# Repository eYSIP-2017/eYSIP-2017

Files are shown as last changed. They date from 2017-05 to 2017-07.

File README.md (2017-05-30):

# eYSIP-2017_DistributedRobotics
## Project Title: 
Distributed Robotic - Multi Swarm Robots

## Project Description:
Understanding the behaviour of swarm robots and swarm intelligence. Building of swarm robots and displaying collective intelligence.

## Problem definition:
Using the swarm robots make the desired shapes of Alphabets. 

## Team: 
### Mentors: 
Ms. Rutuja and Ms. Deepa
### Members: 
Mr. R Hariharan and Mr. Chinmay

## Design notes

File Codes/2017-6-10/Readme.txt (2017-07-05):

The code was a trial to see switching of IR proximity sensor

Platform used : Firebird V (Nex Robotics)

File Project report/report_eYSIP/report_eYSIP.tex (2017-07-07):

\documentclass[a4paper,12pt,oneside]{book}

%-------------------------------Start of the Preable------------------------------------------------
\usepackage[english]{babel}
\usepackage{blindtext}
%packagr for hyperlinks
\usepackage{hyperref}
\hypersetup{
    colorlinks=true,
    linkcolor=blue,
    filecolor=magenta,      
    urlcolor=cyan,
}

\urlstyle{same}
%use of package fancy header
\usepackage{fancyhdr}
\setlength\headheight{26pt}
\fancyhf{}
%\rhead{\includegraphics[width=1cm]{logo}}
\lhead{\rightmark}
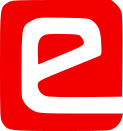
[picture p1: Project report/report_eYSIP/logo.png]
\rhead{}
\fancyfoot[RE, RO]{\thepage}
\fancyfoot[CE, CO]{\href{http://www.e-yantra.org}{www.e-yantra.org}}

\pagestyle{fancy}

%use of package for section title formatting
\usepackage{titlesec}
\titleformat{\chapter}
  {\Large\bfseries} % format
  {}                % label
  {0pt}             % sep
  {\huge}           % before-code
 
%use of package tcolorbox for colorful textbox
\usepackage[most]{tcolorbox}
\tcbset{colback=cyan!5!white,colframe=cyan!75!black,halign title = flush center}

\newtcolorbox{mybox}[1]{colback=cyan!5!white,
colframe=cyan!75!black,fonttitle=\bfseries,
title=\textbf{\Large{#1}}}

%use of package marginnote for notes in margin
\usepackage{marginnote}
\usepackage{tabularx}
%use of packgage watermark for pages
%\usepackage{draftwatermark}
%\SetWatermarkText{\includegraphics{logo}}
\usepackage[scale=2,opacity=0.1,angle=0]{background}
\backgroundsetup{
contents={}
}

%use of newcommand for keywords color
\usepackage{xcolor}
\newcommand{\keyword}[1]{\textcolor{red}{\textbf{#1}}}

%package for inserting pictures
\usepackage{graphicx}

%package for highlighting
\usepackage{color,soul}

%new command for table
\newcommand{\head}[1]{\textnormal{\textbf{#1}}}

%----------------------End of the Preamble---------------------------------------

\begin{document}

%---------------------Title Page------------------------------------------------
\begin{titlepage}
\raggedright
{\Large eYSIP2017\\[1cm]}
{\Huge\scshape\centering Distributed robotics - multi swarm robots \\[.1in]}
\vfill
\hfill\\
\begin{figure}[h!]
	\centering		
\end{figure}	
\hfill\\
\begin{flushright}
{\large Intern 1 Mr. Chinmay C \\}
{\large Intern 2 Mr. R Hariharan \\}
{\large Mentor 1 Ms. Rutuja \\}
{\large Mentor 2 Ms. Deepa \\}
{\large Duration of Internship: $ 22/05/2017-07/07/2017 $ \\}
\end{flushright}

{\itshape 2017, e-Yantra Publication}
\end{titlepage}
%-------------------------------------------------------------------------------

\tableofcontents

\chapter[Distributed robotics - multi swarm robots Hardware manual]{Distributed robotics - multi swarm robots Hardware manual}
\section{Abstract}
Swarm robotics is a field in robotics which implements coordination of multi robot systems which consist of large number of robots having simpler robots. There is a collective behavior that emerges from interactions between robots and interactions of robots with the environment. This behavior is emerged from field of biological studies of fishes, birds, ants, insects, etc. Application of swarm robotics varies from military, aviation to collective behavior of self driving cars. The objective of the project was to build miniaturized swarm bots and develop an algorithm for generic shape formation.

\subsection*{Following points are completed:}
\begin{itemize}
\item Study the concepts of swarm robotics and get familiar
with different robots available 
\item Study the kinematics of differential drive configuration 
\item Selecting appropriate sensors to be added 
\item Designing the PCB 
\item Assembling all the components 
\item Making of Mini bots 
\item Testing of Mini bots
\item Implementing circle formation of asynchronous fat robots with limited visibility in V-REP simulator
\item Developing and implementing generic shape formation algorithm for a system of distributed robots in V-REP simulator
\item Implementing follow the leader swarm behavior on Mini bots
\item Implementing rendezvous swarm behavior on Firebird V robots
\end{itemize}

\chapter[Hardware parts]{Hardware parts}
\begin{itemize}
  \item List of all hardware components are available \href{./COMPONENT LIST/Small_robot_PCB_schematic_WITH_COST.pdf}{here} 
  \item Microcontroller Atmega16 \href{./datasheet/atmega16.pdf}{Datasheet}, {Chip component, Lamington road, Mumbai} 
  \item Hex buffer CD40106 \href{./datasheet/CD40106.pdf}{Datasheet}, {Chip component, Lamington road, Mumbai} 
  \item Motor driver L293D \href{./datasheet/L293.pdf}{Datasheet}, {GALA Electronics, Lamington road, Mumbai} 
  \item Comparator LM158 \href{./datasheet/lm158-n.pdf}{Datasheet}, {Chip component, Lamington road, Mumbai}
  \item Actuators BO motors: 60 rpm 12 volts	
  \item LCD 16x2: GALA Electronics, Lamington road, Mumbai
  \item Position encoders MOC7811: GALA Electronics, Lamington road, Mumbai
  \item ISP programmer STK500v2: \href{}, {Nex robotics}
  \item IR proximity sensors: GALA Electronics, Lamington road, Mumbai
\end{itemize}

\chapter[Softwares used]{Softwares used}
\begin{itemize}
	\item \textbf{Autodesk Eagle 7.6.0}
	\begin{itemize}
		\item \href{https://www.autodesk.com/products/eagle/overview}{Download Eagle}
		\item \href{https://www.youtube.com/user/EAGLECadSoftComputer}{Video tutorials on YouTube}
	\end{itemize}
  \item \textbf{V-rep 3.4.0}
  \begin{itemize}
  	\item \href{https://github.com/eYSIP-2017/eYSIP-2017_DistributedRobotics/blob/master/Documents/Manuals/Understanding_V_REP.pdf}{Understanding V-REP} for beginners
  	\item  \href{http://www.coppeliarobotics.com/downloads.html}{Downloading V-REP}
	\item  \href{http://www.coppeliarobotics.com/resources.html}{For more details on V-REP}
  \end{itemize}
  \item \textbf{Autodesk Fusion 360}
\begin{itemize}
	\item \href{https://www.autodesk.com/products/fusion-360/students-teachers-educators}{To download fusion 360 and get details on it}
\end{itemize}
  \item \textbf{Avrdude}
  \begin{itemize}
  	\item \href{http://www.nongnu.org/avrdude/}{To download Avrdude and get details on it}
  \end{itemize}
\item \textbf{Avrgcc}
 \begin{itemize}
 	\item Worked on windows platform
	\item \href{https://sourceforge.net/projects/winavr/files/}{To download Winavr to get avrgcc}
	\item \href{https://gcc.gnu.org/wiki/avr-gcc}{To understand avrgcc}
\end{itemize}
\item \textbf{Texstudio}
\begin{itemize}
	\item \href{http://www.texstudio.org/}{Download Texstudio}
\end{itemize}
\item \textbf{Git}
\begin{itemize}
	\item \href{https://github.com/eYSIP-2017/eYSIP-2017_DistributedRobotics.git}{Link} to our github repository
	\item \href{https://git-scm.com/}{Download Git}
\end{itemize}
\end{itemize}

\newpage

\chapter{Assembly of hardware}
Refer to our \href{https://github.com/eYSIP-2017/eYSIP-2017_DistributedRobotics/blob/master/Documents/Manuals/Hardware%20Manual/document.pdf}{Hardware Manual} to understand Mini Bot better
\section{Circuit Diagram}
\begin{figure}[h!]
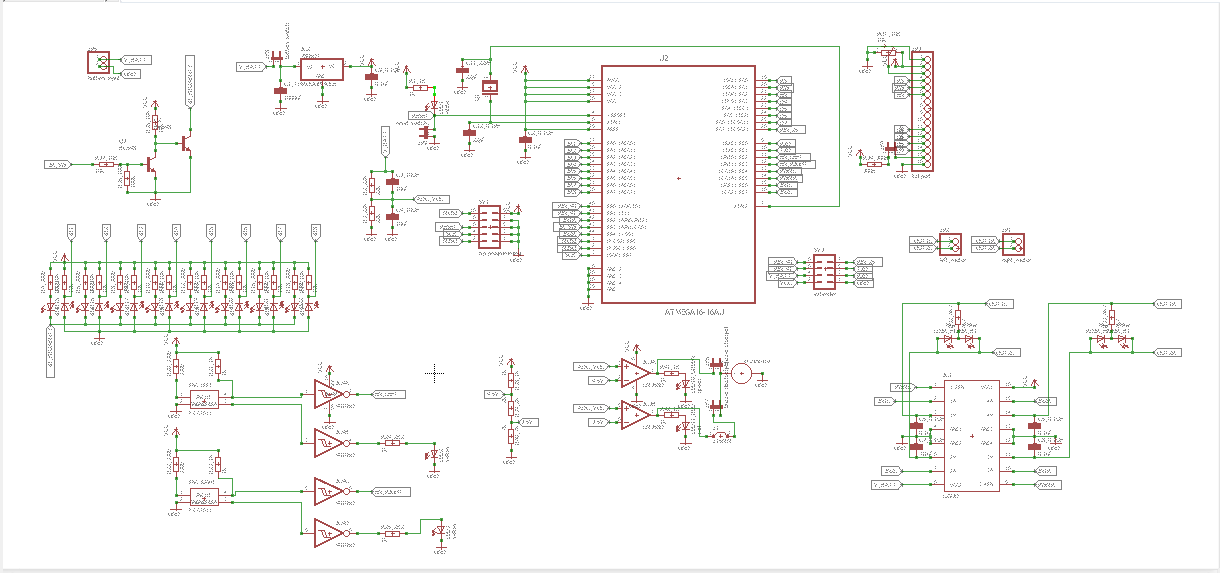
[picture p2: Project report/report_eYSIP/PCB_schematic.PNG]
			
	\caption{Overall schematic of Mini Bot PCB}
\end{figure}
\textbf{Main circuits:}	
\begin{itemize}
	\item L293D motor driver circuits: refer to Motion control section of \href{https://github.com/eYSIP-2017/eYSIP-2017_DistributedRobotics/blob/master/Documents/Manuals/Hardware%20Manual/document.pdf}{Hardware Manual}
	\item Position encoders circuits: refer to Position encoders section of \href{https://github.com/eYSIP-2017/eYSIP-2017_DistributedRobotics/blob/master/Documents/Manuals/Hardware%20Manual/document.pdf}{Hardware Manual}
	\item IR sensors circuits: refer to Infrared proximity and Directional
	light intensity sensors section of \href{https://github.com/eYSIP-2017/eYSIP-2017_DistributedRobotics/blob/master/Documents/Manuals/Hardware%20Manual/document.pdf}{Hardware Manual}
	\item Battery voltage sensor circuits: refer to Battery voltage sensor section of \href{https://github.com/eYSIP-2017/eYSIP-2017_DistributedRobotics/blob/master/Documents/Manuals/Hardware%20Manual/document.pdf}{Hardware Manual}
\end{itemize}
\section{Steps to build Mini Bots}
\subsection*{Step 1: PCB designing and routing}
\begin{figure}[h!]
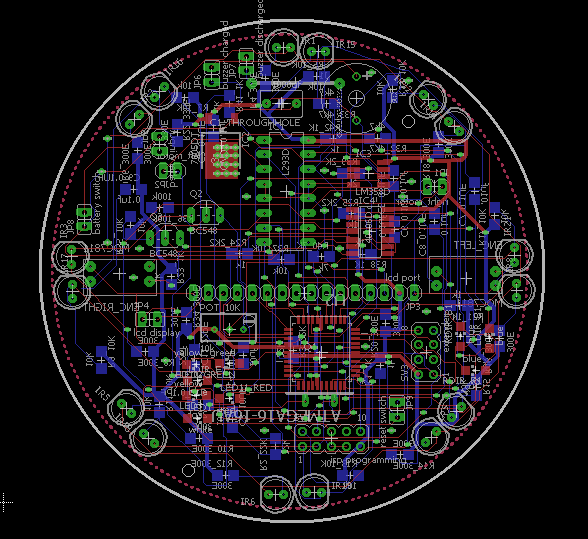
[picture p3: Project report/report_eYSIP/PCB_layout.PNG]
	
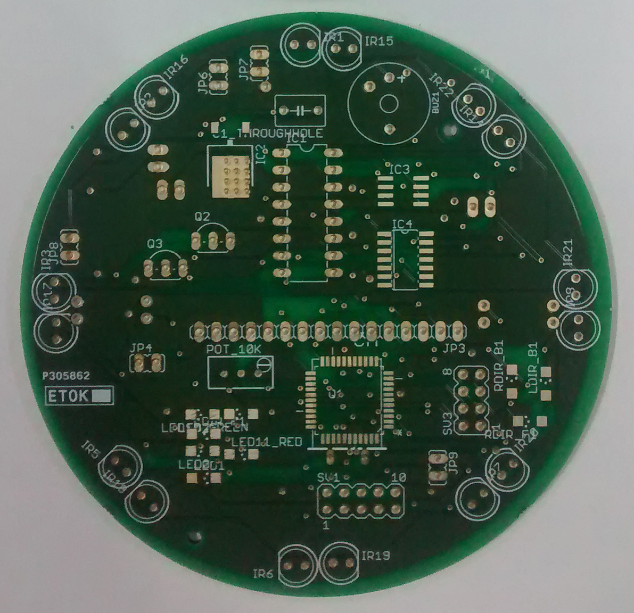
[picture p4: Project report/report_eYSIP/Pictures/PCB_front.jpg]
			
	\caption{Routed and Printed PCB respectively}
\end{figure}	
We used Eagle software for designing the PCB. Gave printing of PCB to PCB power, Circuit Systems India Ltd., Gujarat.
\subsection*{Step 2: Designing of chassis}
We design chassis in Fusion 360 and got it laser cut on 5mm acrylic sheet in Tata Centre, IIT-B. The straight BO motors were fixed with L-clamps and then attached to chassis as shown in figure 4.3. 
\begin{figure}[h!]
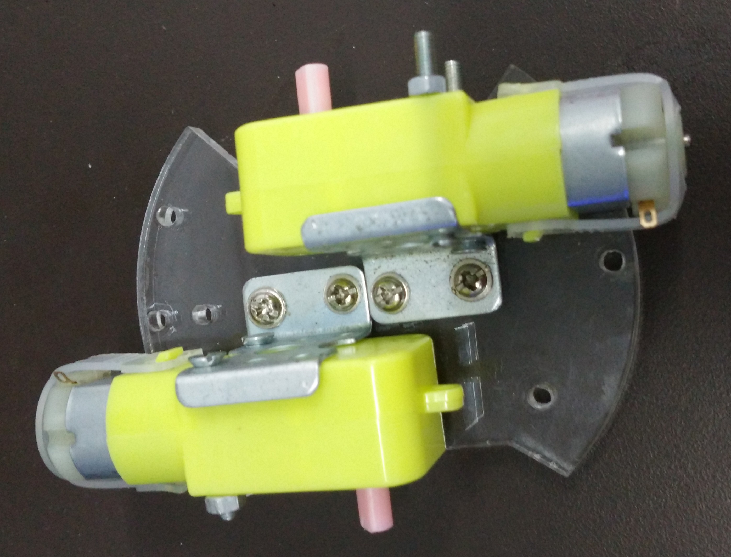
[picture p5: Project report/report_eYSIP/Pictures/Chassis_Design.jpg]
	\centering		
	\caption{Chassis design}
\end{figure}	
       
\subsection*{Step 3: Soldering components on PCB}
Soldering the SMD components onto the PCB, based on the schematics.
\begin{figure}[h!]
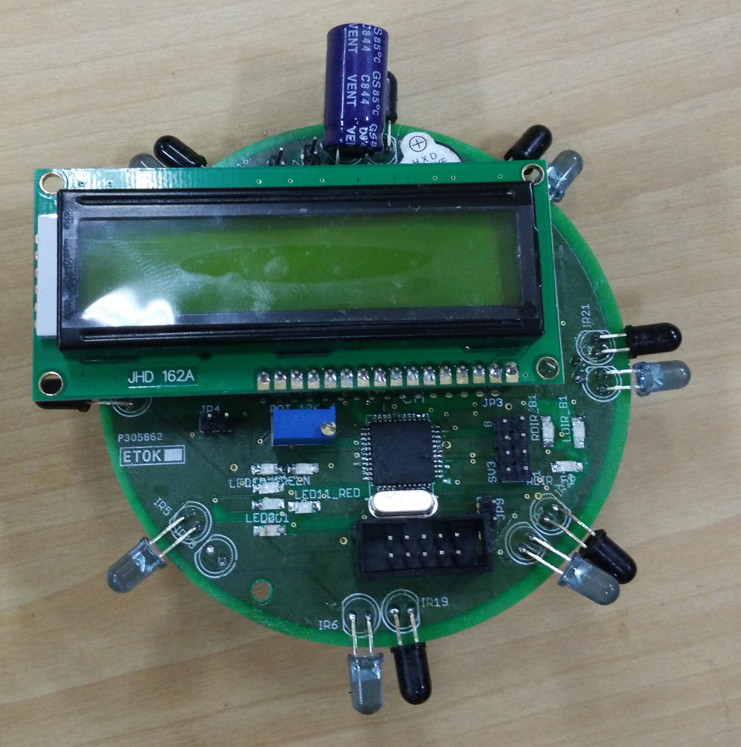
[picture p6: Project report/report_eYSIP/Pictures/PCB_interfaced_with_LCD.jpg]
	\centering
	\caption{Soldered PCB}		
\end{figure}
\subsection*{Step 4: Assembling the robot}
The motors are attached to the chassis and the PCB is screwed to the chassis. The battery connections are appropriately made.
\begin{figure}[h!]
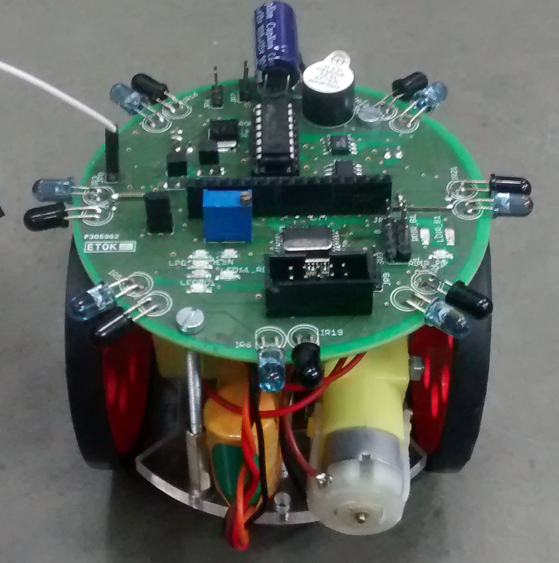
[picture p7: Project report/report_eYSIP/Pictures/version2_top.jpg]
	
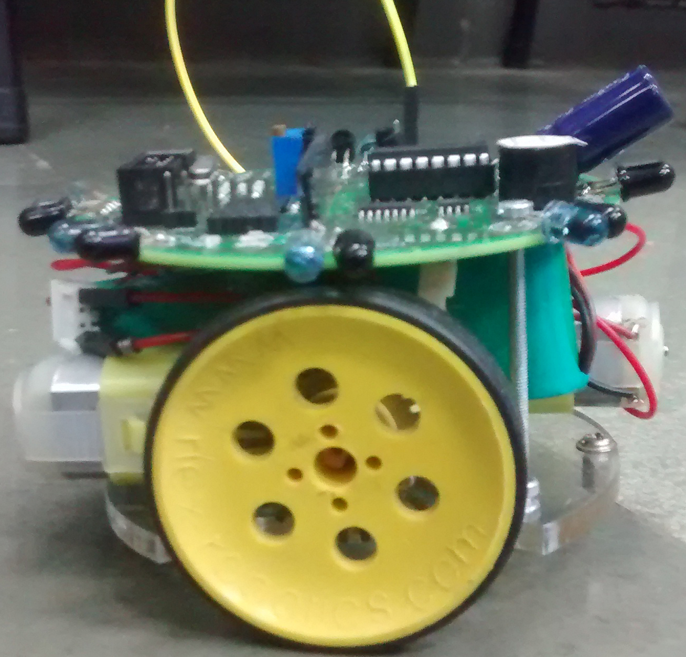
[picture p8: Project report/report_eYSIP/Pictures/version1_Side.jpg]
	
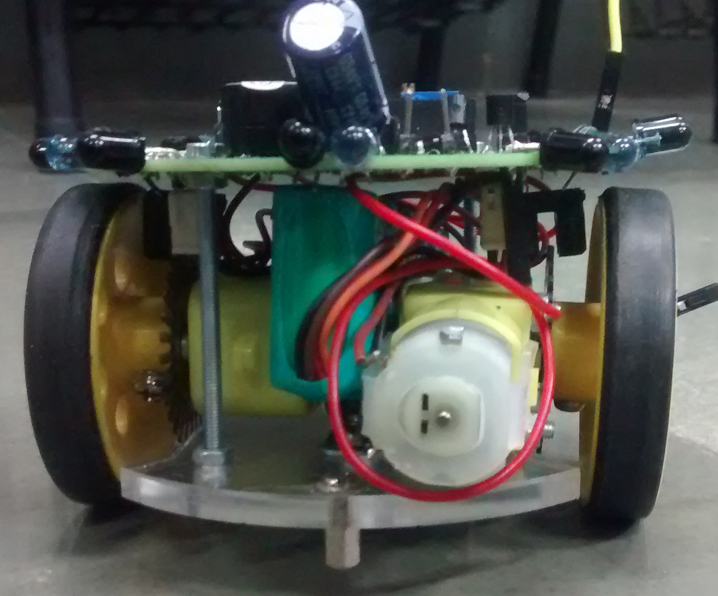
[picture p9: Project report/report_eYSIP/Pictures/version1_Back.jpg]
	
	\caption{Assembled robots}		
\end{figure}	
\hfill\\

\chapter{Software and Code}
\section{Github repository}
\href{https://github.com/eYSIP-2017/eYSIP-2017_DistributedRobotics.git}{Github link} for the repository of code

Github repository contains all the documentation and code of the project worked on. The document folder contains the manuals for hardware components/structure of Mini bots, generic shape formation algorithm for system of distributed robots and a small article to understand the working of V-REP simulator. It also contains video results of the project.

The code folder contains following codes:
\begin{itemize}
	\item C code for P controller for angular control
	\item Embedded C code for rendezvous problem (Firebird V platform)
	\item Eagle EDA project folder
	\item Test code for Mini Bots
	\item V-REP project for circle formation of fat robots
	\item V-REP project for generic shape formation
\end{itemize}

\chapter{Use and Demo}

Videos of the demos can be seen \href{https://github.com/eYSIP-2017/eYSIP-2017_DistributedRobotics/tree/master/Documents/Videos}{here}
\begin{figure}[h!]
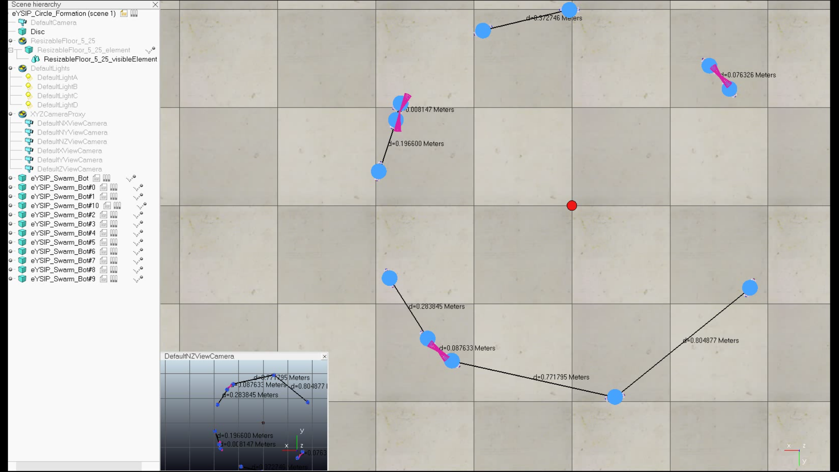
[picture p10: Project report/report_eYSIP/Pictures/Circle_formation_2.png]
	\centering		
	\caption{Multiple robots forming a circle based on algorithm defined in "Circle formation for asynchronous fat robots with limited visibility" in V-REP simulator.}
\end{figure}

\begin{figure}[h!]
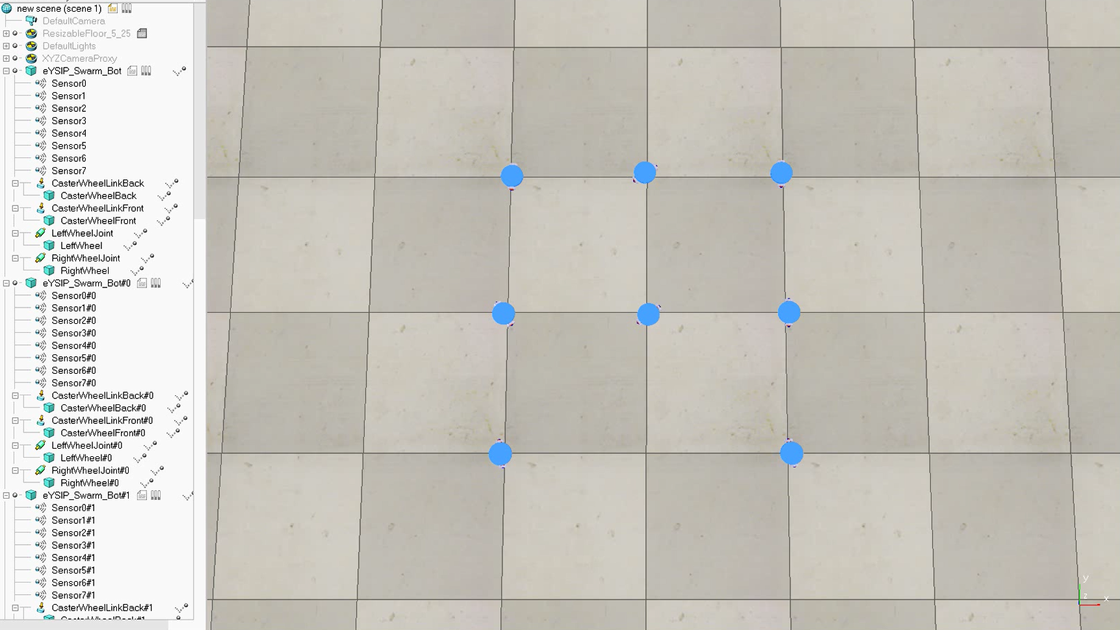
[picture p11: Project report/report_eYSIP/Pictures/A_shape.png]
	\centering		
	\caption{Multiple robots forming shape A based on the algorithm defined in "Generic shape formation algorithm for a system of distributed robots" in V-REP simulator}
\end{figure}

\begin{figure}[h!]
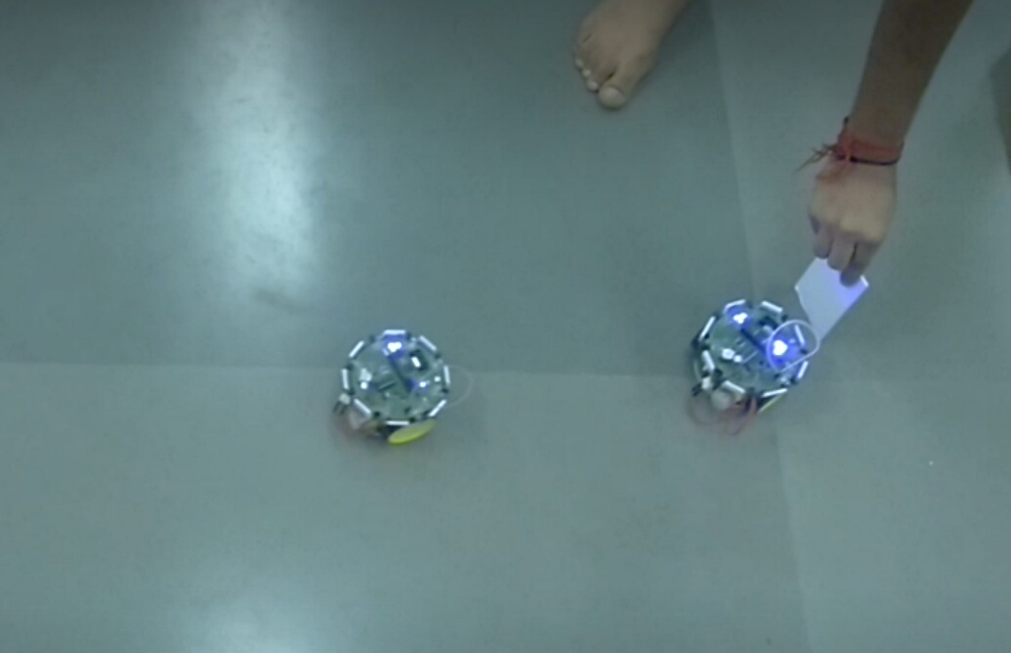
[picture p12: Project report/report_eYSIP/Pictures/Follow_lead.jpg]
	\centering		
	\caption{Follow the leader swarm behavior portrayed by our Mini bots}
\end{figure}	
\newpage
\chapter{Future Work}
\begin{itemize}
	\item Design an outer covering
	\item Implementing circle formation algorithms on Mini bots
	\item Implementing gathering algorithms on Mini bots
	\item Solve shape formation with Mini Bots
	\item Solve collision of homogeneous dynamic swarm robots
	\item Find a better algorithm for tie breaking when many robots approach a single point	
\end{itemize}

\chapter{Bug report and Challenges}
\begin{figure}[h!]
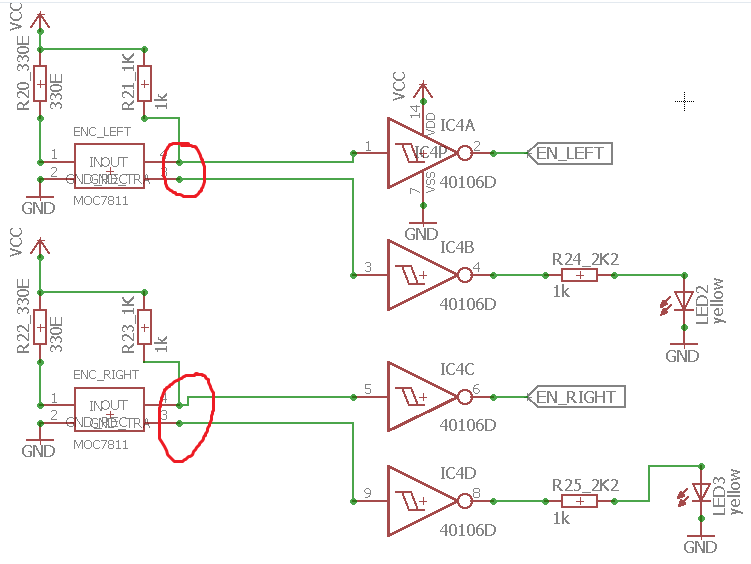
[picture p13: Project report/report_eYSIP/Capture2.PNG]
	
	\caption{Position encoder connection}
\end{figure}

Bugs: Pin 3 of both encoders was supposed to be shorted to ground and connection to buffer connected to led was supposed to be shorted to pin 4\\
Fix: The bug is fixed by shorting pin 3 to ground externally\\

Challenges faced:
\begin{itemize}
	\item Placing components and routing air wires of PCB. 
	\item Reducing overall size of PCB
	\item Understanding different algorithms for circle formation and gathering algorithms for swarm robots to determine a common point for resolving global coordinate system
	\item Soldering SMD components accurately
\end{itemize}

\begin{thebibliography}{li}
\bibitem{wavelan97}
Ayan Dutta, Sruti Gan Chaudhuri, Suparno Datta and Krishnendu Mukhopadhyaya,
{\em Circle formation by asynchronous fat robots with limited visiblity}

\bibitem{wavelan97}
Sruti Gan Chaudhuri and Krishnendu Mukhopadhyaya,
{\em Gathering Asynchronous Transparent Fat Robots}

\bibitem{wavelan97}
Ayan Dutta, Sruti Gan Chaudhuri, Suparno Datta and Krishnendu Mukhopadhyaya,
{\em Circle formation by asynchronous fat robots}

\bibitem{wavelan97}
Swapnil Ghike and Krishnendu Mukhopadhyaya,
{\em A distributed algorithm for pattern formation by autonomous robots, with no agreement on coordinate compass}

\bibitem{wavelan97}
Avik Chatterjee, Sruti Gan Chaudhuri, Krishnendu Mukhopadhyaya,
{\em Gathering asynchronous swarm robots under non uniform limited visibilities}

\bibitem{wavelan97}
Krishnendu Mukhopadhyaya,
{\em Distributed swarm robotics for swarm robots}
\end{thebibliography}

\end{document}

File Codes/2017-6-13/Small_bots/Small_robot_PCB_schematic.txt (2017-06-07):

Partlist exported from C:/Users/Admin/Documents/eagle/Small_bots/Small_robot_PCB_schematic.sch at 02-Jun-17 15:46

Part       Value           Device          Package                  Description                                                                                                                           DESCRIPTION     MF MPN             OC_FARNELL OC_NEWARK PACKAGE  SUPPLIER
C1_1000UF                  C-EUC1206       C1206                    CAPACITOR, European symbol                                                                                                                                                                                     
C2_0.1UF                   C-EUC1206       C1206                    CAPACITOR, European symbol                                                                                                                                                                                     
C3_10UF                    C-EUC1206       C1206                    CAPACITOR, European symbol                                                                                                                                                                                     
C4_10UF                    C-EUC1206       C1206                    CAPACITOR, European symbol                                                                                                                                                                                     
C5_0.1UF                   C-EUC1206       C1206                    CAPACITOR, European symbol                                                                                                                                                                                     
C6_0.1UF                   C-EUC1206       C1206                    CAPACITOR, European symbol                                                                                                                                                                                     
C7_0.1UF                   C-EUC1206       C1206                    CAPACITOR, European symbol                                                                                                                                                                                     
C8_0.1UF                   C-EUC1206       C1206                    CAPACITOR, European symbol                                                                                                                                                                                     
C9_0.1UF                   C-EUC1206       C1206                    CAPACITOR, European symbol                                                                                                                                                                                     
C10_0.1UF                  C-EUC1206       C1206                    CAPACITOR, European symbol                                                                                                                                                                                     
C11_22PF                   C-EUC1206       C1206                    CAPACITOR, European symbol                                                                                                                                                                                     
C12_0.1PF                  C-EUC1206       C1206                    CAPACITOR, European symbol                                                                                                                                                                                     
C13_1000UF                 C-EUC1206       C1206                    CAPACITOR, European symbol                                                                                                                                                                                     
IC1        L293D           L293D           DIL16                    PUSH-PULL 4 CHANNEL DRIVER                                                                                                                               L293D           9589619    56P8249                    
IC2        7805DT          7805DT          TO252                    Positive VOLTAGE REGULATOR                                                                                                                                                                                     
IC3        UA78M33DCY      UA78M33DCY      SOT223                   POSITIVE-VOLTAGE REGULATORS                                                                                                                                                                                    
IC4        40106D          40106D          SO14                     Hex SCHMITT TRIGGER                                                                                                                                                                                            
IR1                        LED5MM          LED5MM                   LED                                                                                                                                                                                                            
IR2                        LED5MM          LED5MM                   LED                                                                                                                                                                                                            
IR3                        LED5MM          LED5MM                   LED                                                                                                                                                                                                            
IR4                        LEDCHIPLED_1206 CHIPLED_1206             LED                                                                                                                                                                                                            
IR5                        LED5MM          LED5MM                   LED                                                                                                                                                                                                            
IR6                        LED5MM          LED5MM                   LED                                                                                                                                                                                                            
IR7                        LED5MM          LED5MM                   LED                                                                                                                                                                                                            
IR8                        LED5MM          LED5MM                   LED                                                                                                                                                                                                            
IR9                        LEDCHIPLED_1206 CHIPLED_1206             LED                                                                                                                                                                                                            
IR10                       LEDCHIPLED_1206 CHIPLED_1206             LED                                                                                                                                                                                                            
IR11                       LEDCHIPLED_1206 CHIPLED_1206             LED                                                                                                                                                                                                            
IR12                       LEDCHIPLED_1206 CHIPLED_1206             LED                                                                                                                                                                                                            
IR13                       LEDCHIPLED_1206 CHIPLED_1206             LED                                                                                                                                                                                                            
IR14                       LED5MM          LED5MM                   LED                                                                                                                                                                                                            
IR15                       LED5MM          LED5MM                   LED                                                                                                                                                                                                            
IR16                       LED5MM          LED5MM                   LED                                                                                                                                                                                                            
IR17                       LED5MM          LED5MM                   LED                                                                                                                                                                                                            
IR18                       LED5MM          LED5MM                   LED                                                                                                                                                                                                            
IR19                       LED5MM          LED5MM                   LED                                                                                                                                                                                                            
IR20                       LED5MM          LED5MM                   LED                                                                                                                                                                                                            
IR21                       LED5MM          LED5MM                   LED                                                                                                                                                                                                            
IR22                       LED5MM          LED5MM                   LED                                                                                                                                                                                                            
IR23                       LEDCHIPLED_1206 CHIPLED_1206             LED                                                                                                                                                                                                            
IR24                       LEDCHIPLED_1206 CHIPLED_1206             LED                                                                                                                                                                                                            
IR25                       LEDCHIPLED_1206 CHIPLED_1206             LED                                                                                                                                                                                                            
IR26                       LEDCHIPLED_1206 CHIPLED_1206             LED                                                                                                                                                                                                            
JP1                        PINHD-1X2       1X02                     PIN HEADER                                                                                                                                                                                                     
JP2                        PINHD-1X2       1X02                     PIN HEADER                                                                                                                                                                                                     
JP3                        PINHD-1X16      1X16                     PIN HEADER                                                                                                                                                                                                     
JP4                        JP1E            JP1                      JUMPER                                                                                                                                                                                                         
LDIR_B1                    LEDCHIPLED_1206 CHIPLED_1206             LED                                                                                                                                                                                                            
LDIR_F1                    LEDCHIPLED_1206 CHIPLED_1206             LED                                                                                                                                                                                                            
LED1                       LEDCHIPLED_1206 CHIPLED_1206             LED                                                                                                                                                                                                            
Q1                         XTAL            Q                        CRYSTAL                                                                                                                                                                                                        
R1_1K                      R-EU_R1206      R1206                    RESISTOR, European symbol                                                                                                                                                                                      
R2_22K                     R-EU_R1206      R1206                    RESISTOR, European symbol                                                                                                                                                                                      
R3_22K                     R-EU_R1206      R1206                    RESISTOR, European symbol                                                                                                                                                                                      
R4_100E                    R-EU_R1206      R1206                    RESISTOR, European symbol                                                                                                                                                                                      
R5_10K                     R-EU_R1206      R1206                    RESISTOR, European symbol                                                                                                                                                                                      
R6_100E                    R-EU_R1206      R1206                    RESISTOR, European symbol                                                                                                                                                                                      
R7_10K                     R-EU_R1206      R1206                    RESISTOR, European symbol                                                                                                                                                                                      
R8_100E                    R-EU_R1206      R1206                    RESISTOR, European symbol                                                                                                                                                                                      
R9_\10K                    R-EU_R1206      R1206                    RESISTOR, European symbol                                                                                                                                                                                      
R10_100E                   R-EU_R1206      R1206                    RESISTOR, European symbol                                                                                                                                                                                      
R11_10K                    R-EU_R1206      R1206                    RESISTOR, European symbol                                                                                                                                                                                      
R12_100E                   R-EU_R1206      R1206                    RESISTOR, European symbol                                                                                                                                                                                      
R13_10K                    R-EU_R1206      R1206                    RESISTOR, European symbol                                                                                                                                                                                      
R14_100E                   R-EU_R1206      R1206                    RESISTOR, European symbol                                                                                                                                                                                      
R15_10K                    R-EU_R1206      R1206                    RESISTOR, European symbol                                                                                                                                                                                      
R16_100E                   R-EU_R1206      R1206                    RESISTOR, European symbol                                                                                                                                                                                      
R17_10K                    R-EU_R1206      R1206                    RESISTOR, European symbol                                                                                                                                                                                      
R18_100E                   R-EU_R1206      R1206                    RESISTOR, European symbol                                                                                                                                                                                      
R19_10K                    R-EU_R1206      R1206                    RESISTOR, European symbol                                                                                                                                                                                      
R20_330                    R-EU_R1206      R1206                    RESISTOR, European symbol                                                                                                                                                                                      
R21_1K                     R-EU_R1206      R1206                    RESISTOR, European symbol                                                                                                                                                                                      
R22_1_330                  R-EU_R1206      R1206                    RESISTOR, European symbol                                                                                                                                                                                      
R23_1K                     R-EU_R1206      R1206                    RESISTOR, European symbol                                                                                                                                                                                      
R24_2K2                    R-EU_R1206      R1206                    RESISTOR, European symbol                                                                                                                                                                                      
R25_2K2                    R-EU_R1206      R1206                    RESISTOR, European symbol                                                                                                                                                                                      
R26_2K2                    R-EU_R1206      R1206                    RESISTOR, European symbol                                                                                                                                                                                      
R27_2K2                    R-EU_R1206      R1206                    RESISTOR, European symbol                                                                                                                                                                                      
R28_2K2                    R-EU_R1206      R1206                    RESISTOR, European symbol                                                                                                                                                                                      
R29_2K2                    R-EU_R1206      R1206                    RESISTOR, European symbol                                                                                                                                                                                      
R30_2K2                    R-EU_R1206      R1206                    RESISTOR, European symbol                                                                                                                                                                                      
R31_2K2                    R-EU_R1206      R1206                    RESISTOR, European symbol                                                                                                                                                                                      
R32_4K7                    R-EU_R1206      R1206                    RESISTOR, European symbol                                                                                                                                                                                      
R33_4K7                    R-EU_R1206      R1206                    RESISTOR, European symbol                                                                                                                                                                                      
R34_100E                   R-EU_R1206      R1206                    RESISTOR, European symbol                                                                                                                                                                                      
R35_10K                    R-EU_R1206      R1206                    RESISTOR, European symbol                                                                                                                                                                                      
R36_10K2                   R-EU_R1206      R1206                    RESISTOR, European symbol                                                                                                                                                                                      
RDIR_B1                    LEDCHIPLED_1206 CHIPLED_1206             LED                                                                                                                                                                                                            
RDIR_F1                    LEDCHIPLED_1206 CHIPLED_1206             LED                                                                                                                                                                                                            
SV1                        MA05-2          MA05-2                   PIN HEADER                                                                                                                                                               unknown    unknown                    
U$1        MOC7811         MOC7811         THROUGH_HOLE_NORMAL      MOC7811 is a slotted opto isolator module, with an IR transmitter and a photodiode mounted on it. Performs Non-Contact Object Sensing                                                                          
U$2        MOC7811         MOC7811         THROUGH_HOLE_NORMAL      MOC7811 is a slotted opto isolator module, with an IR transmitter and a photodiode mounted on it. Performs Non-Contact Object Sensing                                                                          
U1         ATMEGA2560-16AU ATMEGA2560-16AU QFP50P1600X1600X120-100N Microcontroller                                                                                                                       Microcontroller    ATMEGA2560-16AU 1288330    23M5051   LQFP-100 ATMEL   
XB1        XBEE            XBEE            XBEE                     XBee (TM) /XBee-PRO(TM) OEM RF Modules                                                                                                                   XBP24-Z7UIT-004 1751799    34R5507

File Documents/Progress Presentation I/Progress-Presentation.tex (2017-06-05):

\documentclass[10pt, a4paper]{beamer}

\usetheme{Berkeley}
\usecolortheme{sidebartab}
\usepackage{parskip}
\usepackage{graphicx}

\setlength{\parindent}{15pt}

\begin{document}
	\setbeamertemplate{sidebar left}{}
	\title{Progress Presentation-I}
	\subtitle{e-Yantra Summer Intership-2016 \\ Distributed Robotics - Multi Swarm Robots}
	\author{Chinmay C\\R Hariharan\\
	\textbf{Mentors}:\\ Ms. Rutuja and Ms. Deepa}
	\institute{IIT Bombay}
	\date{\today}
	%\addtobeamertemplate{sidebar left}{}{\includegraphics[scale = 0.3]{logowithtext.png}}
	\frame{\titlepage}

\setbeamertemplate{sidebar left}[sidebar theme]
\section{Overview of Project}
\begin{frame}{Overview of Project}
	\begin{itemize}
		\setlength\itemsep{0em}
		\item \textbf{Project Name}
			\begin{itemize} 
				\setlength\itemsep{-1em}
				\item Distributed Robotics - Multi Swarm Robots
			\end{itemize}
		\item \textbf{Objective} 
			\begin{itemize}
				\setlength\itemsep{-0.7em}
				\item \textbf{Bulid minibots} which have capabilities to sense its surrounding and communicate with its neighbouring robots
				\item \textbf{Shape formation} using the minibots
			\end{itemize}
		\item \textbf{Deliverables}
			\begin{itemize}
				\setlength\itemsep{-0.7em}
				\item \textbf{Five Minibots} that can portray swarm behaviours 
				\item Implement/Develop an \textbf{algorithm} to form shapes using the robots
			\end{itemize}
	\end{itemize}
\end{frame}

\section{Overview of Task}
\begin{frame}{Overview of Task}
	\begin{center}
		\begin{tabular}{|p{8cm}|p{1cm}|} 
			\hline
			\textbf{TASK} & \textbf{DAYS} \\ 
			\hline
			Study the concepts of swarm robotics and get familiar with different robots available & 3 \\ 
			\hline
			Make the Minibots: & \\ 
			\hline
			Study the kinematics of differential drive configuration & 3 \\ 
			\hline
			Select appropriate sensors to be added: & 3 \\ 
			\hline
			Design the pcbs & 3 \\ 
			\hline
			Assemble all the components & 4 \\ 
			\hline
			Test the robots & 3 \\ 
			\hline
			Solve rendezvous problem using homogenous controller gain & 2 \\ 
			\hline
			Solve rendezvous problem using heterogenous controller gain & 2 \\ 
			\hline
			Shape formation & 4 \\ 
			\hline
			Documentation & 5 \\ 
			\hline		
		\end{tabular}
	\end{center}
\end{frame}

\section{Task Accomplised}
\begin{frame}{Task Accomplised}
	\begin{itemize}
		\setlength\itemsep{-0.5em}
		\item Understanding the fundamentals of swarm robotics
		\item Learning motion kinematics and inverse kinematics for mapping distance and angle to the position
		\item Designing PCB:
		\begin{itemize}
			\setlength\itemsep{-1em}
			\item Components and shape (8cm dia) finalization
			\item Understanding eagle software
			\item Designing schematics
			\item Placing parts in PCB layout
			\item Routing the PCB, generating Bill of materials and gerber files
			\item Finalizing PCB design
		\end{itemize}
		\item Solved rendezvous problem using Firebird V robots
		\item Developed an algorithm for line formation by swarm robots
	\end{itemize}
\end{frame}

\section{Basic Design of Minibot}
\begin{frame}{Basic Desgin of Minibot}
	\begin{figure}
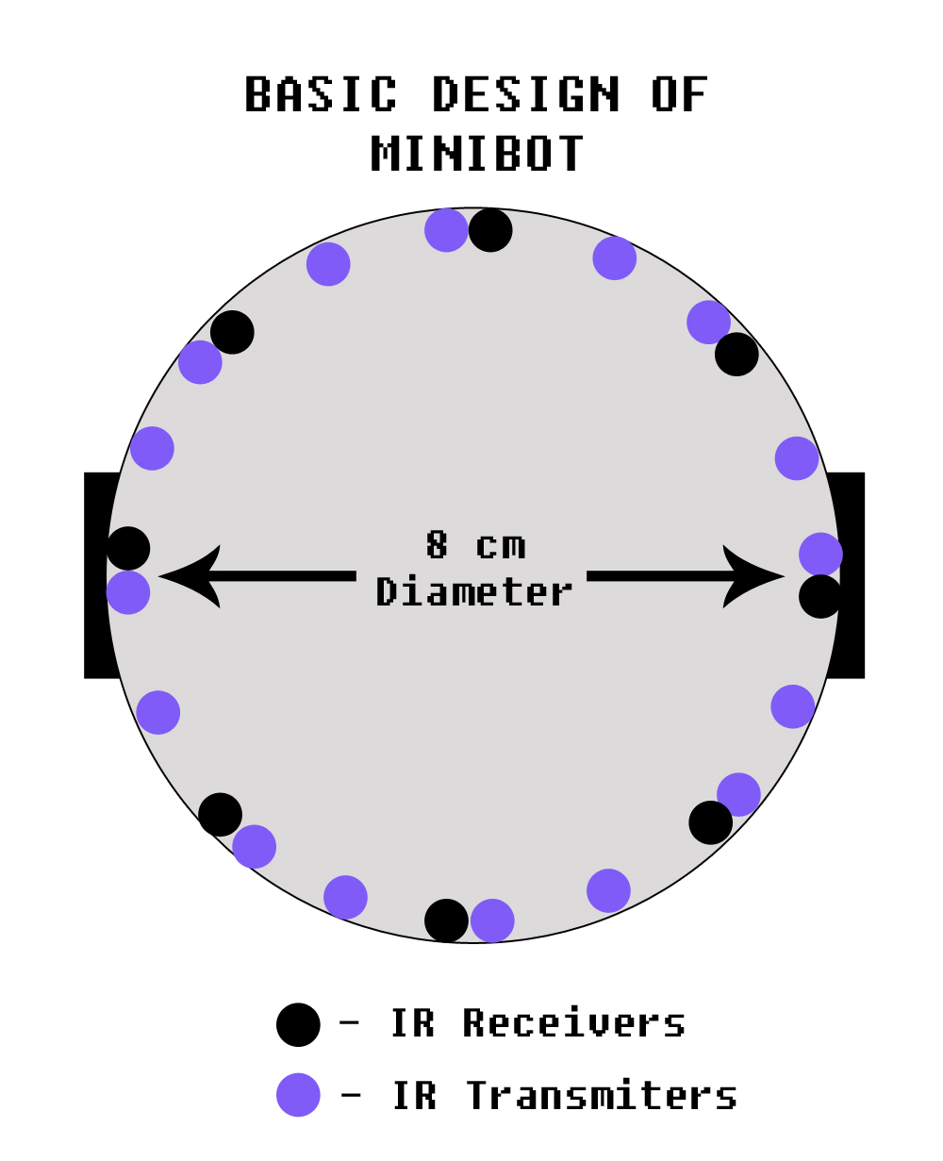
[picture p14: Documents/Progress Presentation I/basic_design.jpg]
		
		\label{fig:Design}
	\end{figure}
\end{frame}

\section{PCB Design and Schematics}
\begin{frame}{PCB Design and Schematic}
\begin{figure}
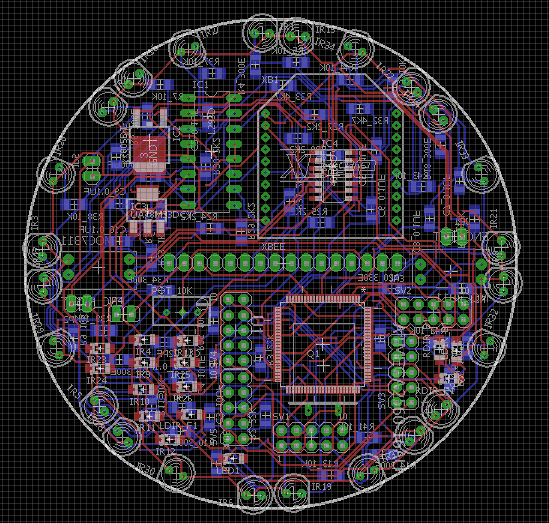
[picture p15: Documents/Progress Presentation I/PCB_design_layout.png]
	
	\label{fig:PCB Design}
\end{figure}
\end{frame}

\section{Challenges Faced}
\begin{frame}{Challenges Faced}
	\begin{itemize}
		\item Miniaturizing the design of minirobot
		\item Designing of PCB with the constraints in size
		\item Routing double layered PCB
		\item Mapping IR reading to actual distances
		\item Designing line formation algorithm with respect to relative positions of robots
	\end{itemize}
\end{frame}

\section{Future Plans}
\begin{frame}{Future Plans}
	\begin{itemize}
		\item Desinging and building chassis for the minibots
		\item Printing of PCB and soldering parts
		\item Reading on already existing shape forming algorithms in swarm robots
		\item Developing an algorithm for forming regular shapes
		\item Further implementing the same for alphabets
	\end{itemize}
\end{frame}

\section{Thank You}
\begin{frame}{Thank You}
	\begin{tabular}{p{3cm} c c}
	 	& THANK YOU !!! &
	\end{tabular}
\end{frame}
\end{document}

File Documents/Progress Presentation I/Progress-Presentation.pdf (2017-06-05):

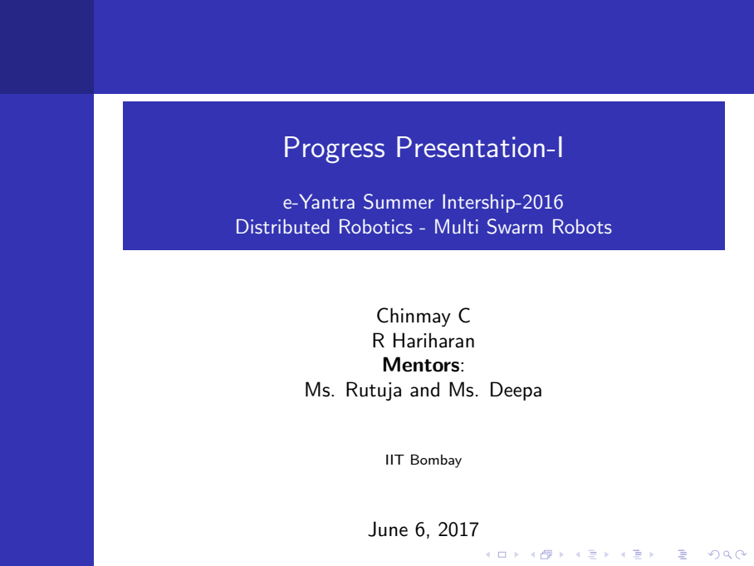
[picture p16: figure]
Progress Presentation-I; e-Yantra Summer Intership-2016; Chinmay C R Hariharan Mentors: Ms. Rutuja and Ms. Deepa; IIT Bombay; June 6, 2017

# Distributed Robotics - Multi Swarm Robots

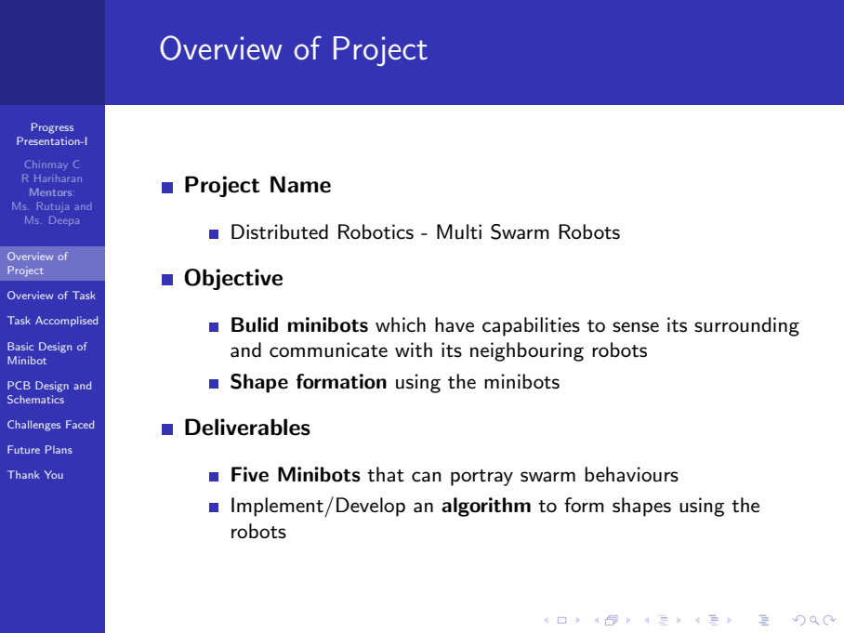
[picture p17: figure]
Progress Presentation-I; Chinmay C R Hariharan Mentors: Ms. Rutuja and Ms. Deepa; Overview of Project; Overview of Task; Task Accomplised; Basic Design of Minibot; PCB Design and Schematics; Challenges Faced; Future Plans; Thank You; Project Name; Objective; Shape formation using the minibots; Deliverables; robots

# Distributed Robotics - Multi Swarm Robots

# Bulid minibots which have capabilities to sense its surrounding and communicate with its neighbouring robots

# Five Minibots that can portray swarm behaviours

# Implement/Develop an algorithm to form shapes using the

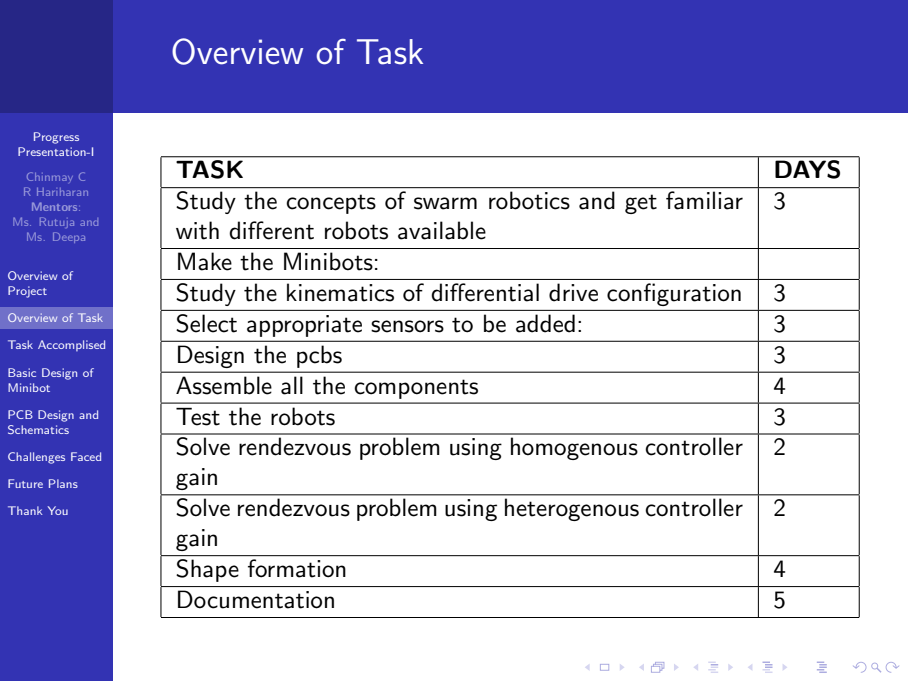
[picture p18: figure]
Progress Presentation-I; Chinmay C R Hariharan Mentors: Ms. Rutuja and Ms. Deepa; Overview of Project; Overview of Task; Task Accomplised; Basic Design of Minibot; PCB Design and Schematics; Challenges Faced; Future Plans; Thank You; TASK; DAYS; Make the Minibots:; Design the pcbs; Assemble all the components; Test the robots; Shape formation; Documentation

Study the concepts of swarm robotics and get familiar with different robots available | 3
Study the kinematics of differential drive configuration | 3
Select appropriate sensors to be added: | 3
Solve rendezvous problem using homogenous controller gain | 2
Solve rendezvous problem using heterogenous controller gain | 2

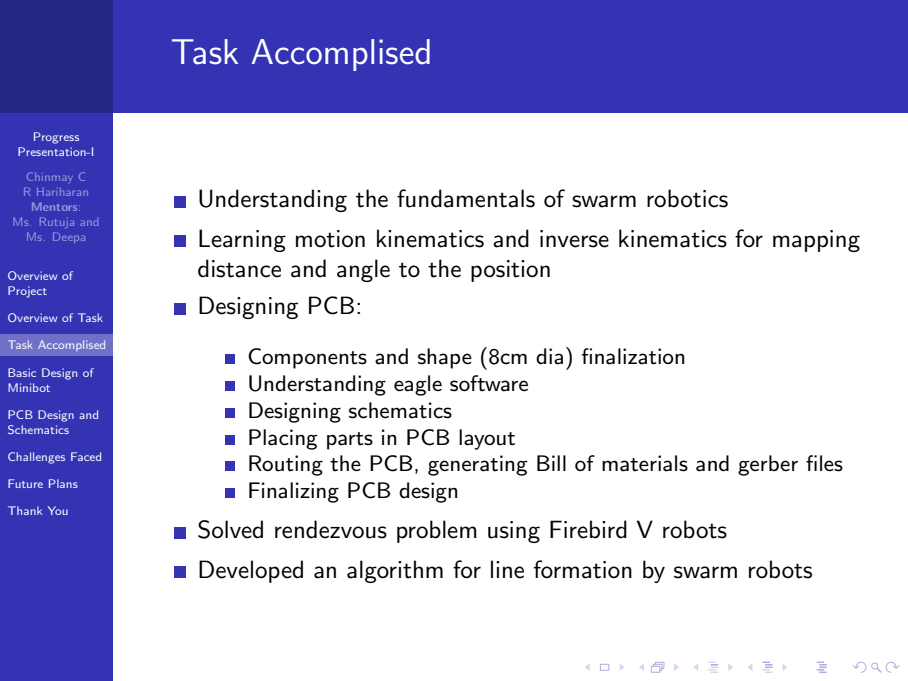
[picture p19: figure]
Progress Presentation-I; Chinmay C R Hariharan Mentors: Ms. Rutuja and Ms. Deepa; Overview of Project; Overview of Task; Task Accomplised; Basic Design of Minibot; PCB Design and Schematics; Challenges Faced; Future Plans; Thank You; distance and angle to the position; Designing PCB:; Understanding eagle software Designing schematics Placing parts in PCB layout; Finalizing PCB design

# Understanding the fundamentals of swarm robotics

# Learning motion kinematics and inverse kinematics for mapping

# Components and shape (8cm dia) finalization

# Routing the PCB, generating Bill of materials and gerber files

# Solved rendezvous problem using Firebird V robots

# Developed an algorithm for line formation by swarm robots

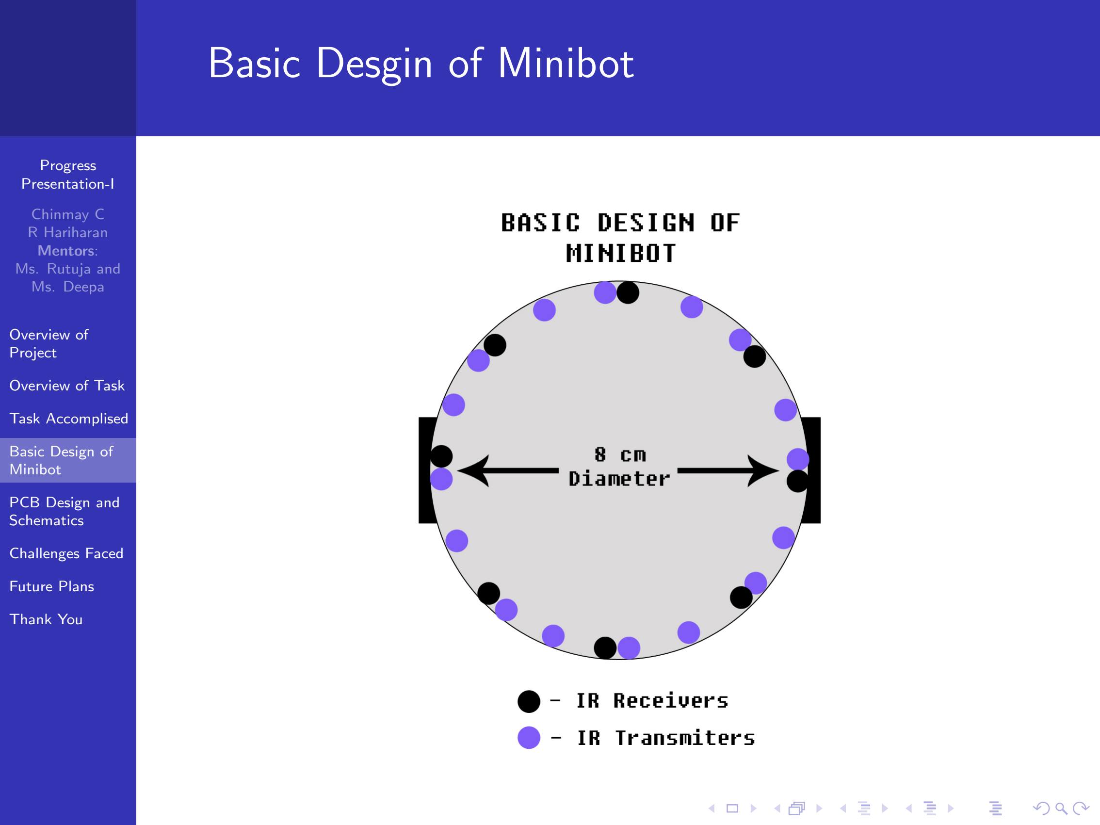
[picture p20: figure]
Progress Presentation-I; Chinmay C R Hariharan Mentors: Ms. Rutuja and Ms. Deepa; Overview of Project; Overview of Task; Task Accomplised; Basic Design of Minibot; PCB Design and Schematics; Challenges Faced; Future Plans; Thank You; Basic Desgin of Minibot

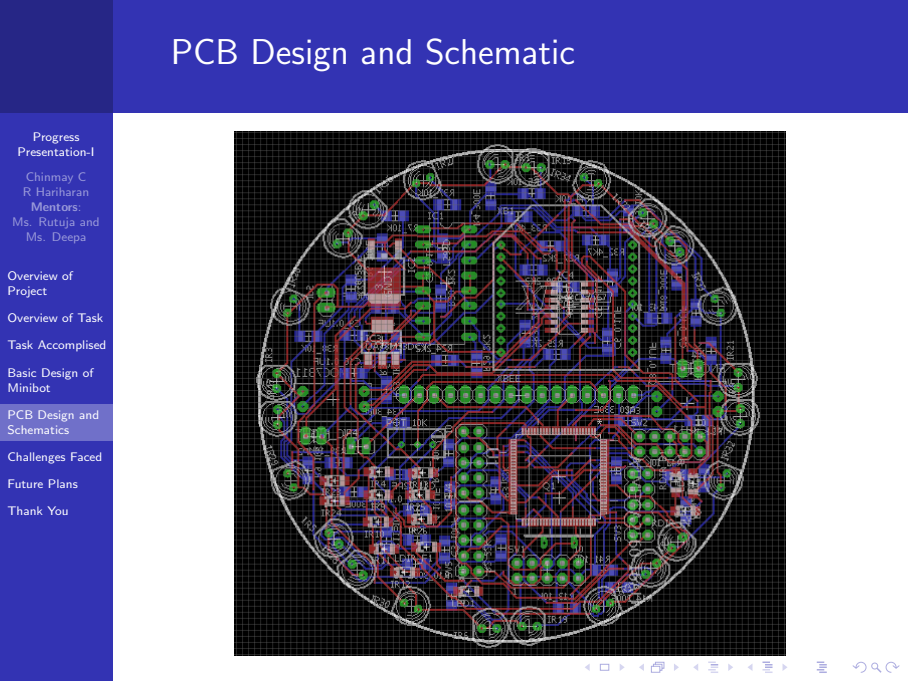
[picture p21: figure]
Progress Presentation-I; Chinmay C R Hariharan Mentors: Ms. Rutuja and Ms. Deepa; Overview of Project; Overview of Task; Task Accomplised; Basic Design of Minibot; PCB Design and Schematics; Challenges Faced; Future Plans; Thank You; PCB Design and Schematic

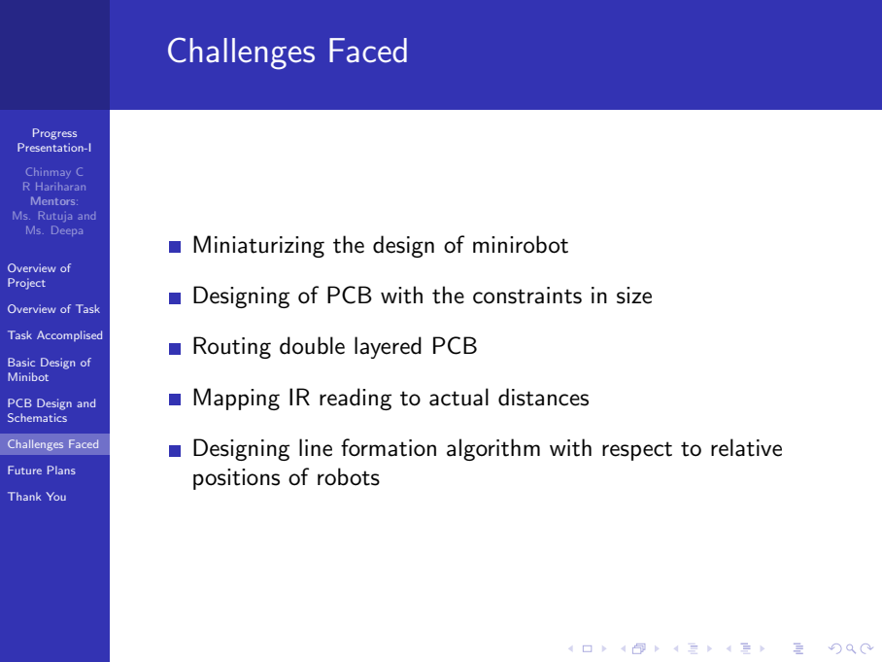
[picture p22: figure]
Progress Presentation-I; Chinmay C R Hariharan Mentors: Ms. Rutuja and Ms. Deepa; Overview of Project; Overview of Task; Task Accomplised; Basic Design of Minibot; PCB Design and Schematics; Challenges Faced; Future Plans; Thank You; Miniaturizing the design of minirobot; Routing double layered PCB; Mapping IR reading to actual distances; positions of robots

# Designing of PCB with the constraints in size

# Designing line formation algorithm with respect to relative

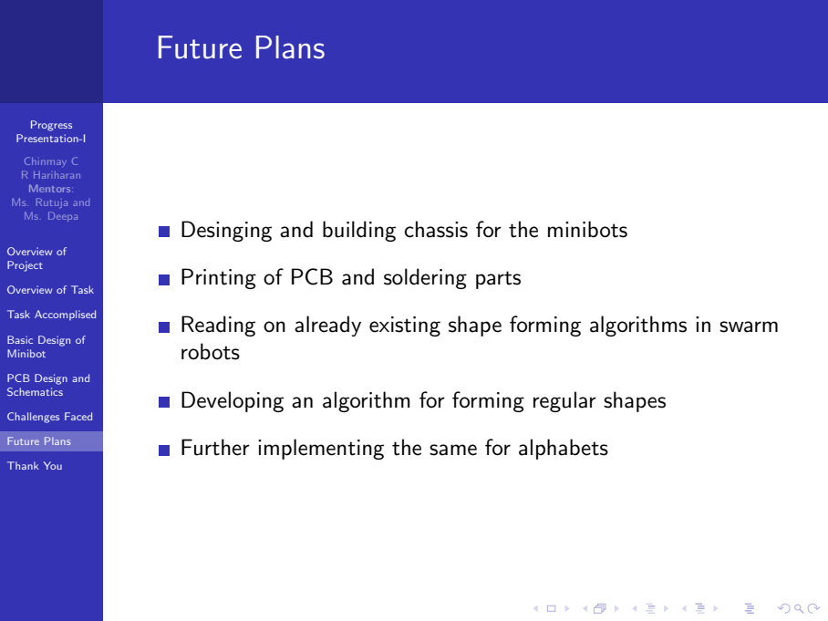
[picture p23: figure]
Progress Presentation-I; Chinmay C R Hariharan Mentors: Ms. Rutuja and Ms. Deepa; Overview of Project; Overview of Task; Task Accomplised; Basic Design of Minibot; PCB Design and Schematics; Challenges Faced; Future Plans; Thank You; Printing of PCB and soldering parts; robots

# Desinging and building chassis for the minibots

# Reading on already existing shape forming algorithms in swarm

# Developing an algorithm for forming regular shapes

# Further implementing the same for alphabets

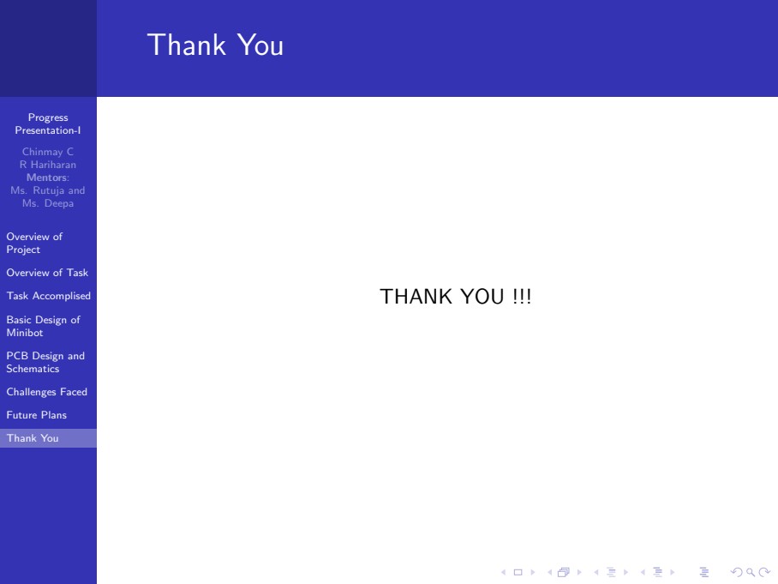
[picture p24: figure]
Progress Presentation-I; Chinmay C R Hariharan Mentors: Ms. Rutuja and Ms. Deepa; Overview of Project; Overview of Task; Task Accomplised; Basic Design of Minibot; PCB Design and Schematics; Challenges Faced; Future Plans; Thank You; THANK YOU !!!

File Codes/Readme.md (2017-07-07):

# Contents of the folder
2017-5-27 : P-Controller for angular velocity of a robot (C Code)

2017-5-30 : C Code for Randezvous Problem 

2017-5-31 : Embedded C Code for Randezvous Problem (Firebird V)

2017-6-01 : Mini Bots eagle design folder and line forming algorithm C Code

2017-6-07 : Mini Bots eagle design folder - Updated

2017-6-09 : Mini Bots eagle design folder - Updated

2017-6-10 : Embedded C Code to check the properties of switching IR (Firebird V)

2017-6-13 : Mini Bots eagle design folder - Updated

2017-6-19 : V-REP documents for P-Controller for a mobile robot to goto any co-ordinate

2017-6-26 : V-REP documents for implementation of circle formation of fat robots algorithm
 
2017-6-27 : All the test codes for our Mini Robot

2017-7-05 : V-REP documents for implementation generic shape formation algorithm

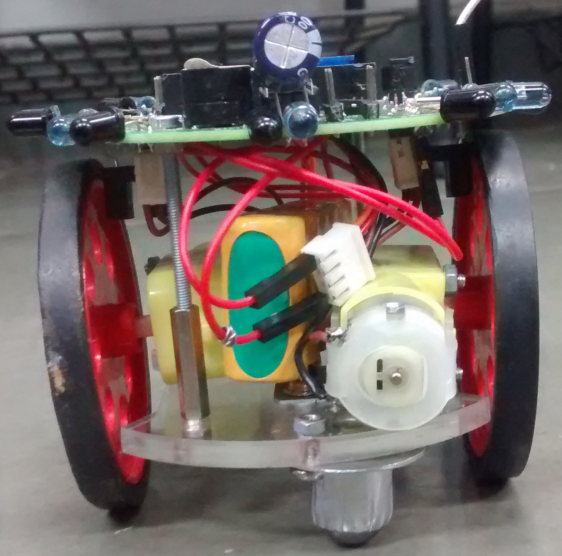
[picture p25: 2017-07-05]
Project report/report_eYSIP/Pictures/version2_back.jpg

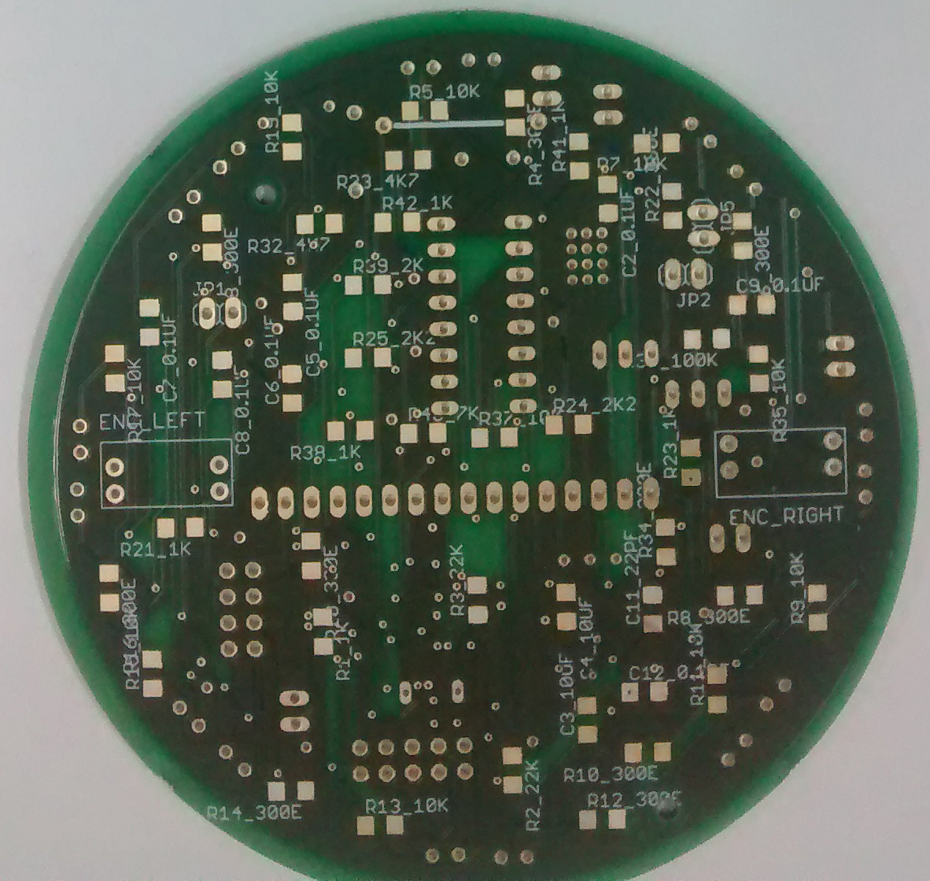
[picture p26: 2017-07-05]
Project report/report_eYSIP/Pictures/PCB_back.jpg

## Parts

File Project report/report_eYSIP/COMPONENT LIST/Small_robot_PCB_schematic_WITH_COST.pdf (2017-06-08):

Small_robot_PCB_schematic

Page 1

Part | Value | Place | Package | COST (RS) | Description
C7_0.1UF | .01uf | CHIP COMPONENT | C1206 | 12CAPACITOR, European symbol
C2_0.1UF | 0.1uf | CHIP COMPONENT | C1206 | 12CAPACITOR, European symbol
C5_0.1UF | 0.1uf | CHIP COMPONENT | C1206 | 12CAPACITOR, European symbol
C6_0.1UF | 0.1uf | CHIP COMPONENT | C1206 | 12CAPACITOR, European symbol
C8_0.1UF | 0.1uf | CHIP COMPONENT | C1206 | 12CAPACITOR, European symbol
C9_0.1UF | 0.1uf | CHIP COMPONENT | C1206 | 12CAPACITOR, European symbol
R36_100K | 100k | CHIP COMPONENT | R1206 | 12RESISTOR, European symbol
R11_10K | 10k | CHIP COMPONENT | R1206 | 12RESISTOR, European symbol
R13_10K | 10k | CHIP COMPONENT | R1206 | 12RESISTOR, European symbol
R15_10K | 10k | CHIP COMPONENT | R1206 | 12RESISTOR, European symbol
R17_10K | 10k | CHIP COMPONENT | R1206 | 12RESISTOR, European symbol
R19_10K | 10k | CHIP COMPONENT | R1206 | 12RESISTOR, European symbol
R35_10K | 10k | CHIP COMPONENT | R1206 | 12RESISTOR, European symbol
R37_10K | 10k | CHIP COMPONENT | R1206 | 12RESISTOR, European symbol
R5_10K | 10k | CHIP COMPONENT | R1206 | 12RESISTOR, European symbol
R7_10K | 10k | CHIP COMPONENT | R1206 | 12RESISTOR, European symbol
R9_10K | 10k | CHIP COMPONENT | R1206 | 12RESISTOR, European symbol
C3_10UF | 10uf | CHIP COMPONENT | C1206 | 12CAPACITOR, European symbol
C4_10UF | 10uf | CHIP COMPONENT | C1206 | 12CAPACITOR, European symbol
R1_1K | 1k | CHIP COMPONENT | R1206 | 12RESISTOR, European symbol
R21_1K | 1k | CHIP COMPONENT | R1206 | 12RESISTOR, European symbol
R23_1K | 1k | CHIP COMPONENT | R1206 | 12RESISTOR, European symbol
R38_1K | 1k | CHIP COMPONENT | R1206 | 12RESISTOR, European symbol
R41_1K | 1k | CHIP COMPONENT | R1206 | 12RESISTOR, European symbol
R42_1K | 1k | CHIP COMPONENT | R1206 | 12RESISTOR, European symbol
R2_22K | 22k | CHIP COMPONENT | R1206 | 12RESISTOR, European symbol
R3_22K | 22k | CHIP COMPONENT | R1206 | 12RESISTOR, European symbol
C11_22PF | 22pf | CHIP COMPONENT | C1206 | 12CAPACITOR, European symbol
C12_0.1PF | 22pf | CHIP COMPONENT | C1206 | 12CAPACITOR, European symbol
R39_2K | 2k | CHIP COMPONENT | R1206 | 12RESISTOR, European symbol

Small_robot_PCB_schematic

Page 2

R24_2K2 | 2k2 | CHIP COMPONENT | R1206 | 12RESISTOR, European symbol
R25_2K2 | 2k2 | CHIP COMPONENT | R1206 | 12RESISTOR, European symbol
R10_300E | 300E | CHIP COMPONENT | R1206 | 12RESISTOR, European symbol
R12_300E | 300E | CHIP COMPONENT | R1206 | 12RESISTOR, European symbol
R14_300E | 300E | CHIP COMPONENT | R1206 | 12RESISTOR, European symbol
R16_300E | 300E | CHIP COMPONENT | R1206 | 12RESISTOR, European symbol
R18_300E | 300E | CHIP COMPONENT | R1206 | 12RESISTOR, European symbol
R34_300E | 300E | CHIP COMPONENT | R1206 | 12RESISTOR, European symbol
R4_300E | 300E | CHIP COMPONENT | R1206 | 12RESISTOR, European symbol
R6_300E | 300E | CHIP COMPONENT | R1206 | 12RESISTOR, European symbol
R8_300E | 300E | CHIP COMPONENT | R1206 | 12RESISTOR, European symbol
R20_330E | 330E | CHIP COMPONENT | R1206 | 12RESISTOR, European symbol
R22_330E | 330E | CHIP COMPONENT | R1206 | 12RESISTOR, European symbol
IC4 | 40106D | CHIP COMPONENT | SO14 | 12 Hex SCHMITT TRIGGER
R32_4K7 | 4k7 | CHIP COMPONENT | R1206 | 12RESISTOR, European symbol
R33_4K7 | 4k7 | CHIP COMPONENT | R1206 | 12RESISTOR, European symbol
R40_7K | 7k | CHIP COMPONENT | R1206 | 12RESISTOR, European symbol
U2 | ATMEGA16-16AU | CHIP COMPONENT | QFP80P1200X1200X120-44N | 12 | 8-bit Microcontroller
LDIR_B1 | blue | CHIP COMPONENT | CHIPLED_1206 | 12 | LED
LDIR_F1 | blue | CHIP COMPONENT | CHIPLED_1206 | 12 | LED
RDIR_B1 | blue | CHIP COMPONENT | CHIPLED_1206 | 12 | LED
RDIR_F1 | blue | CHIP COMPONENT | CHIPLED_1206 | 12 | LED
LED10_GREEN | green | CHIP COMPONENT | CHIPLED_1206 | 12 | LED
IC3 | LM358D | CHIP COMPONENT | SO08 | OP AMP also LM158; LM258; LM2904 12
LED11_RED | red | CHIP COMPONENT | CHIPLED_1206 | 12 | LED
LED1 | white | CHIP COMPONENT | CHIPLED_1206 | 12 | LED
LED2 | yellow | CHIP COMPONENT | CHIPLED_1206 | 12 | LED
LED3 | yellow | CHIP COMPONENT | CHIPLED_1206 | 12 | LED
C1_THROUGHHOLE | 1000uf | GALA ELECTRONICS | C050-045X075 | 4CAPACITOR, European symbol
POT_10K | 10k | GALA ELECTRONICS | RTRIMT93YA | 10 | Trimm resistor
IC2 | 7805DT | GALA ELECTRONICS | TO252 | 20Positive VOLTAGE REGULATOR

Small_robot_PCB_schematic

Page 3

JP5 | battery input | GALA ELECTRONICS | 1X02 | 10 | PIN HEADER
Q2 | BC548 | GALA ELECTRONICS | TO92-EBC | 10 | NPN Transistor
Q3 | BC548 | GALA ELECTRONICS | TO92-EBC | 10 | NPN Transistor
SV3 | extender | GALA ELECTRONICS | MA04-2 | 10 | PIN HEADER
SV1 | isp programming | GALA ELECTRONICS | MA05-2 | 10 | PIN HEADER
BUZ1 | KS-12065D03YA | GALA ELECTRONICS | BZ2-7.6-D12.0XH6.5MM | 10 | 312010004
IC1 | L293D | GALA ELECTRONICS | DIL16 | PUSH-PULL 4 CHANNEL DRIVER 40
JP3 | lcd port | GALA ELECTRONICS | 1X16 | 10 | PIN HEADER
JP2 | left_motor | GALA ELECTRONICS | 1X02 | 10 | PIN HEADER
ENC_LEFT | MOC7811 | GALA ELECTRONICS | THROUGH_HOLE_NORMAL | 10
ENC_RIGHT | MOC7811 | GALA ELECTRONICS | THROUGH_HOLE_NORMAL | 10
JP9 | reset switch | GALA ELECTRONICS | JP1 | 10 | JUMPER
JP1 | right_motor | GALA ELECTRONICS | 1X02 | 10 | PIN HEADER
IR1 | | GALA ELECTRONICS | LED5MM | 1 | LED
IR14 | | GALA ELECTRONICS | LED5MM | 1 | LED
IR15 | | GALA ELECTRONICS | LED5MM | 1 | LED
IR16 | | GALA ELECTRONICS | LED5MM | 1 | LED
IR17 | | GALA ELECTRONICS | LED5MM | 1 | LED
IR18 | | GALA ELECTRONICS | LED5MM | 1 | LED
IR19 | | GALA ELECTRONICS | LED5MM | 1 | LED
IR2 | | GALA ELECTRONICS | LED5MM | 1 | LED
IR20 | | GALA ELECTRONICS | LED5MM | 1 | LED
IR21 | | GALA ELECTRONICS | LED5MM | 1 | LED
IR22 | | GALA ELECTRONICS | LED5MM | 1 | LED

MOC7811 is a slotted opto isolator module, with an IR transmitter and a photodiode mounted on it. Performs Non-Contact Object Sensing
MOC7811 is a slotted opto isolator module, with an IR transmitter and a photodiode mounted on it. Performs Non-Contact Object Sensing

Small_robot_PCB_schematic

Page 4

IR3 | GALA ELECTRONICS | LED5MM | 1 | LED
IR5 | GALA ELECTRONICS | LED5MM | 1 | LED
IR6 | GALA ELECTRONICS | LED5MM | 1 | LED
IR7 | GALA ELECTRONICS | LED5MM | 1 | LED
IR8 | GALA ELECTRONICS | LED5MM | 1 | LED
LCD | GALA ELECTRONICS | 120
Q1 | GALA ELECTRONICS | Q | 5 | CRYSTAL
BO MOTOR | GALA ELECTRONICS | 2 | 70
CASTER WHEEL | GALA ELECTRONICS | 2 | 20
L – CLAMPS | GALA ELECTRONICS | 2 | 20
JP8 | battery switch | NIL | JP1 | JUMPER
JP6 | buzzer charged | NIL | JP1 | JUMPER
JP7 | buzzer discharged | NIL | JP1 | JUMPER
JP4 | lcd display | NIL | JP1 | JUMPER
COST PER BOT | 1141
TOTAL COST | 5705

Small_robot_PCB_schematic

Page

5

Small_robot_PCB_schematic

Page

6

Small_robot_PCB_schematic

Page 7

Small_robot_PCB_schematic

Page 8

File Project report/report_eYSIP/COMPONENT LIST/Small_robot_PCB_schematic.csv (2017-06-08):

Part | Value | Place | Package | Description
C7_0.1UF | .01uf | CHIP COMPONENT | C1206 | CAPACITOR, European symbol
C2_0.1UF | 0.1uf | CHIP COMPONENT | C1206 | CAPACITOR, European symbol
C5_0.1UF | 0.1uf | CHIP COMPONENT | C1206 | CAPACITOR, European symbol
C6_0.1UF | 0.1uf | CHIP COMPONENT | C1206 | CAPACITOR, European symbol
C8_0.1UF | 0.1uf | CHIP COMPONENT | C1206 | CAPACITOR, European symbol
C9_0.1UF | 0.1uf | CHIP COMPONENT | C1206 | CAPACITOR, European symbol
R36_100K | 100k | CHIP COMPONENT | R1206 | RESISTOR, European symbol
R11_10K | 10k | CHIP COMPONENT | R1206 | RESISTOR, European symbol
R13_10K | 10k | CHIP COMPONENT | R1206 | RESISTOR, European symbol
R15_10K | 10k | CHIP COMPONENT | R1206 | RESISTOR, European symbol
R17_10K | 10k | CHIP COMPONENT | R1206 | RESISTOR, European symbol
R19_10K | 10k | CHIP COMPONENT | R1206 | RESISTOR, European symbol
R35_10K | 10k | CHIP COMPONENT | R1206 | RESISTOR, European symbol
R37_10K | 10k | CHIP COMPONENT | R1206 | RESISTOR, European symbol
R5_10K | 10k | CHIP COMPONENT | R1206 | RESISTOR, European symbol
R7_10K | 10k | CHIP COMPONENT | R1206 | RESISTOR, European symbol
R9_10K | 10k | CHIP COMPONENT | R1206 | RESISTOR, European symbol
C3_10UF | 10uf | CHIP COMPONENT | C1206 | CAPACITOR, European symbol
C4_10UF | 10uf | CHIP COMPONENT | C1206 | CAPACITOR, European symbol
R1_1K | 1k | CHIP COMPONENT | R1206 | RESISTOR, European symbol
R21_1K | 1k | CHIP COMPONENT | R1206 | RESISTOR, European symbol
R23_1K | 1k | CHIP COMPONENT | R1206 | RESISTOR, European symbol
R38_1K | 1k | CHIP COMPONENT | R1206 | RESISTOR, European symbol
R41_1K | 1k | CHIP COMPONENT | R1206 | RESISTOR, European symbol
R42_1K | 1k | CHIP COMPONENT | R1206 | RESISTOR, European symbol
R2_22K | 22k | CHIP COMPONENT | R1206 | RESISTOR, European symbol
R3_22K | 22k | CHIP COMPONENT | R1206 | RESISTOR, European symbol
C11_22PF | 22pf | CHIP COMPONENT | C1206 | CAPACITOR, European symbol
C12_0.1PF | 22pf | CHIP COMPONENT | C1206 | CAPACITOR, European symbol
R39_2K | 2k | CHIP COMPONENT | R1206 | RESISTOR, European symbol
R24_2K2 | 2k2 | CHIP COMPONENT | R1206 | RESISTOR, European symbol
R25_2K2 | 2k2 | CHIP COMPONENT | R1206 | RESISTOR, European symbol
R10_300E | 300E | CHIP COMPONENT | R1206 | RESISTOR, European symbol
R12_300E | 300E | CHIP COMPONENT | R1206 | RESISTOR, European symbol
R14_300E | 300E | CHIP COMPONENT | R1206 | RESISTOR, European symbol
R16_300E | 300E | CHIP COMPONENT | R1206 | RESISTOR, European symbol
R18_300E | 300E | CHIP COMPONENT | R1206 | RESISTOR, European symbol
R34_300E | 300E | CHIP COMPONENT | R1206 | RESISTOR, European symbol
R4_300E | 300E | CHIP COMPONENT | R1206 | RESISTOR, European symbol
R6_300E | 300E | CHIP COMPONENT | R1206 | RESISTOR, European symbol
R8_300E | 300E | CHIP COMPONENT | R1206 | RESISTOR, European symbol
R20_330E | 330E | CHIP COMPONENT | R1206 | RESISTOR, European symbol
R22_330E | 330E | CHIP COMPONENT | R1206 | RESISTOR, European symbol
IC4 | 40106D | CHIP COMPONENT | SO14 | Hex SCHMITT TRIGGER
R32_4K7 | 4k7 | CHIP COMPONENT | R1206 | RESISTOR, European symbol
R33_4K7 | 4k7 | CHIP COMPONENT | R1206 | RESISTOR, European symbol
R40_7K | 7k | CHIP COMPONENT | R1206 | RESISTOR, European symbol
U2 | ATMEGA16-16AU | CHIP COMPONENT | QFP80P1200X1200X120-44N | 8-bit Microcontroller
LDIR_B1 | blue | CHIP COMPONENT | CHIPLED_1206 | LED
LDIR_F1 | blue | CHIP COMPONENT | CHIPLED_1206 | LED
RDIR_B1 | blue | CHIP COMPONENT | CHIPLED_1206 | LED
RDIR_F1 | blue | CHIP COMPONENT | CHIPLED_1206 | LED
LED10_GREEN | green | CHIP COMPONENT | CHIPLED_1206 | LED
IC3 | LM358D | CHIP COMPONENT | SO08 | OP AMP also LM158; LM258; LM2904
LED11_RED | red | CHIP COMPONENT | CHIPLED_1206 | LED
LED1 | white | CHIP COMPONENT | CHIPLED_1206 | LED
LED2 | yellow | CHIP COMPONENT | CHIPLED_1206 | LED
LED3 | yellow | CHIP COMPONENT | CHIPLED_1206 | LED
C1_THROUGHHOLE | 1000uf | GALA ELECTRONICS | C050-045X075 | CAPACITOR, European symbol
POT_10K | 10k | GALA ELECTRONICS | RTRIMT93YA | Trimm resistor
IC2 | 7805DT | GALA ELECTRONICS | TO252 | Positive VOLTAGE REGULATOR
JP5 | battery input | GALA ELECTRONICS | 1X02 | PIN HEADER
Q2 | BC548 | GALA ELECTRONICS | TO92-EBC | NPN Transistor
Q3 | BC548 | GALA ELECTRONICS | TO92-EBC | NPN Transistor
SV3 | extender | GALA ELECTRONICS | MA04-2 | PIN HEADER
SV1 | isp programming | GALA ELECTRONICS | MA05-2 | PIN HEADER
BUZ1 | KS-12065D03YA | GALA ELECTRONICS | BZ2-7.6-D12.0XH6.5MM | 312010004
IC1 | L293D | GALA ELECTRONICS | DIL16 | PUSH-PULL 4 CHANNEL DRIVER
JP3 | lcd port | GALA ELECTRONICS | 1X16 | PIN HEADER
JP2 | left_motor | GALA ELECTRONICS | 1X02 | PIN HEADER
ENC_LEFT | MOC7811 | GALA ELECTRONICS | THROUGH_HOLE_NORMAL | MOC7811 is a slotted opto isolator module, with an IR transmitter and a photodiode mounted on it. Performs Non-Contact Object Sensing
ENC_RIGHT | MOC7811 | GALA ELECTRONICS | THROUGH_HOLE_NORMAL | MOC7811 is a slotted opto isolator module, with an IR transmitter and a photodiode mounted on it. Performs Non-Contact Object Sensing
JP9 | reset switch | GALA ELECTRONICS | JP1 | JUMPER
JP1 | right_motor | GALA ELECTRONICS | 1X02 | PIN HEADER
IR1 |  | GALA ELECTRONICS | LED5MM | LED
IR14 |  | GALA ELECTRONICS | LED5MM | LED
IR15 |  | GALA ELECTRONICS | LED5MM | LED
IR16 |  | GALA ELECTRONICS | LED5MM | LED
IR17 |  | GALA ELECTRONICS | LED5MM | LED
IR18 |  | GALA ELECTRONICS | LED5MM | LED
IR19 |  | GALA ELECTRONICS | LED5MM | LED
IR2 |  | GALA ELECTRONICS | LED5MM | LED
IR20 |  | GALA ELECTRONICS | LED5MM | LED
IR21 |  | GALA ELECTRONICS | LED5MM | LED
IR22 |  | GALA ELECTRONICS | LED5MM | LED
IR3 |  | GALA ELECTRONICS | LED5MM | LED
IR5 |  | GALA ELECTRONICS | LED5MM | LED
IR6 |  | GALA ELECTRONICS | LED5MM | LED
IR7 |  | GALA ELECTRONICS | LED5MM | LED
IR8 |  | GALA ELECTRONICS | LED5MM | LED
LCD |  | GALA ELECTRONICS
Q1 |  | GALA ELECTRONICS | Q | CRYSTAL
BO MOTOR |  | GALA ELECTRONICS | 2
CASTER WHEEL |  | GALA ELECTRONICS | 2
L – CLAMPS |  | GALA ELECTRONICS | 2
JP8 | battery switch | NIL | JP1 | JUMPER
JP6 | buzzer charged | NIL | JP1 | JUMPER
JP7 | buzzer discharged | NIL | JP1 | JUMPER
JP4 | lcd display | NIL | JP1 | JUMPER
 |  |  | COST PER BOT
 |  |  | TOTAL COST

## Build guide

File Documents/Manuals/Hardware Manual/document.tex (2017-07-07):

\documentclass[a4paper,12pt,oneside]{book}

%-------------------------------Start of the Preable------------------------------------------------
\usepackage[english]{babel}
\usepackage{blindtext}
%packagr for hyperlinks
\usepackage{hyperref}
\hypersetup{
	colorlinks=true,
	linkcolor=blue,
	filecolor=magenta,      
	urlcolor=cyan,
}

\urlstyle{same}
%use of package fancy header
\usepackage{fancyhdr}
\setlength\headheight{26pt}
\fancyhf{}
%\rhead{\includegraphics[width=1cm]{logo}}
\lhead{\rightmark}
\rhead{}
\fancyfoot[RE, RO]{\thepage}
\fancyfoot[CE, CO]{\href{http://www.e-yantra.org}{www.e-yantra.org}}

\pagestyle{fancy}

%use of package for section title formatting
\usepackage{titlesec}
\titleformat{\chapter}
{\Large\bfseries} % format
{}                % label
{0pt}             % sep
{\huge}           % before-code

%use of package tcolorbox for colorful textbox
\usepackage[most]{tcolorbox}
\tcbset{colback=cyan!5!white,colframe=cyan!75!black,halign title = flush center}

\newtcolorbox{mybox}[1]{colback=cyan!5!white,
	colframe=cyan!75!black,fonttitle=\bfseries,
	title=\textbf{\Large{#1}}}

%use of package marginnote for notes in margin
\usepackage{marginnote}

%use of packgage watermark for pages
%\usepackage{draftwatermark}
%\SetWatermarkText{\includegraphics{logo}}
\usepackage[scale=2,opacity=0.1,angle=0]{background}
\backgroundsetup{
	contents={}
}

%use of newcommand for keywords color
\usepackage{xcolor}
\newcommand{\keyword}[1]{\textcolor{red}{\textbf{#1}}}

%package for inserting pictures
\usepackage{graphicx}

%package for highlighting
\usepackage{color,soul}

%new command for table
\newcommand{\head}[1]{\textnormal{\textbf{#1}}}

\usepackage[export]{adjustbox}

%----------------------End of the Preamble---------------------------------------

\begin{document}

%---------------------Title Page------------------------------------------------
\begin{titlepage}
	\raggedright
	{\Large eYSIP2017\\[1cm]}
	{\Huge\scshape\centering Distributed robotics - multi swarm robots \\ Hardware manual\\[.1in]}
	\vfill
		\hfill\\
	\begin{figure}[h!]
				
	\end{figure}	
	\hfill\\
	\begin{flushright}
		{\large Intern 1 Mr. Chinmay C \\}
		{\large Intern 2 Mr. R Hariharan \\}
		{\large Mentor 1 Ms. Rutuja \\}
		{\large Mentor 2 Ms. Deepa \\}
		{\large Duration of Internship: $ 22/05/2017-07/07/2017 $ \\}
	\end{flushright}
	
	{\itshape 2017, e-Yantra Publication}
\end{titlepage}
	
\tableofcontents

	\chapter{Introduction}
	Thanks for choosing the Mini bots mobile robot platform. Mini bots will give you good
	exposure to the world of swarm robotics and embedded systems. Thanks to its innovative architecture
	and adoption of the ‘Open Source Philosophy’ in its software and hardware design, you will be
	able to create and contribute to complex applications that run on this platform, helping you
	acquire expertise as you spend more time with them.\\
	\textbf{Safety precautions:}
	\begin{enumerate}
	\item Robot’s electronics is static sensitive. Use robot in static free environment.
	\item If robot’s battery low buzzer starts beeping, immediately charge the batteries.
	\item To prevent fire hazard, do not expose the equipment to rain or moisture.
	\item Refrain from dismantling the unit or any of its accessories once robot is assembled.
	\item Never allow NiMH battery to deep discharge.
	\item Mount all the components with correct polarity.
	\item Keep wheels away from long hair or fur.
	\item Keep the robot away from the wet areas. Contact with water will damage the robot.
	\item To avoid risks of fall, keep your robot in a stable position.
	\item Do not attach any connectors while robot is powered ON.
	\item Never leave the robot powered ON when it is not in use.
\end{enumerate}
\textbf{Inappropriate Operation:}\\
Inappropriate operation can damage your robot. Inappropriate operation includes, but is not
limited to:
	\begin{enumerate}		
	\item Dropping the robot, running it off an edge, or otherwise operating it in an irresponsible
	manner.
	\item Interfacing new hardware without considering compatibility
	\item Overloading the robot above its payload capacity.
	\item Exposing the robot to wet environments.
	\item Continuing to run the robot after hair, yarn, string, or any other item has become
	entangled in the robot’s axles or wheels.
	\item All other forms of inappropriate operation.
	\item Using robot in areas prone to static electricity.
\end{enumerate}
	
	\chapter{Mini Bots Block Diagram}
	
	\begin{figure}[h!]
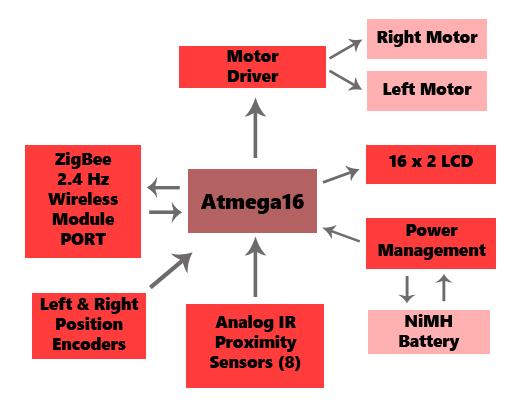
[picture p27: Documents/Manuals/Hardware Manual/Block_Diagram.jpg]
		\centering
		\caption{Block diagram of hardware}
	\end{figure}
	\hfill\\
	\chapter{Mini bots technical specification}
	\begin{enumerate}
		\item{\textbf{\large{Microcontroller:}}\\ATMEL ATMEGA16}\
		\item{\textbf{\large{Sensors:}}\\Eight IR proximity sensors\\Two Position Encoders\\Battery voltage sensing}
		\item{\textbf{\large{Indicators:}}\\2 x 16 Characters LCD\\
			Indicator LEDs\\
			Buzzer\\
			Battery low indication}\\
		\item{\textbf{\large{Locomotion:}}\\Two 60 RPM DC geared motors\\Top Speed: 66cm/second\\}
		\item{\textbf{\large{Operational Modes:}}\\Standalone (Autonomous Control)\\
			Distributed (multi robot communication)\\} 
		\item{\textbf{\large{Communication:}}\\Simplex infrared communication (From infrared to robot)\\
		Zigbee communication (port provided)\\} 
		\item{\textbf{\large{Dimensions:}}\\Diameter: 15cm\\
			Height: 7cm\\} 
		\item{\textbf{\large{Power:}}\\6 AA size NiMH rechargeable batteries} 
	\end{enumerate}
	\hfill\\	
	\underline{\textbf{\Large{Top view of PCB}}}
	\begin{figure}[h!]
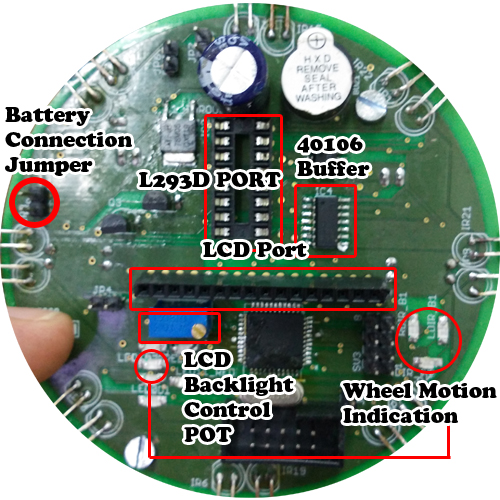
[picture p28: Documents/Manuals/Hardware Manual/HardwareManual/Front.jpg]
		
		\caption{Top view of PCB}
	\end{figure}
	\hfill\\
	
	\chapter{Powering up Mini bots}
	\begin{itemize}
		\item{Mini bots are powered by six AA sized NiMH rechargeable batteries. 2.1Ah battery gives about
			two hour battery operation. Battery is available as preassembled 6 cell pack or robot has AA
			sized 6 cell battery holder.}
		\item{Before connecting the battery pack or inserting batteries in the socket, make sure that 	battery connection jumper of the robot is not put. You need to charge the battery before first use. Use any AC adaptor / SMPS	which can give accurate 12V DC and 1Amp current.}
	\end{itemize}
	
	\begin{itemize}
	\item {Mini bots are powered by 6 NiMH rechargeable batteries of 0.8Ah and above capacity. When it is
	fully discharged voltage drops to about 7V. Battery pack should not be discharged below 6V (1V
	per cell) to extend the battery life. Mini bots have onboard smart battery detector which monitors
	battery status. Nickel Metal Hydride batteries must be recharged externally.\\
	Power management block on the Mini bots performs following functions.\\
	1. Battery low warning in case battery is below critical level\\
	2. Regulated supply for onboard payload.\\
	3. Battery charging when robot is powered off and external battery charger is
	connected.\\}
	\end{itemize}

	\begin{figure}[h!]
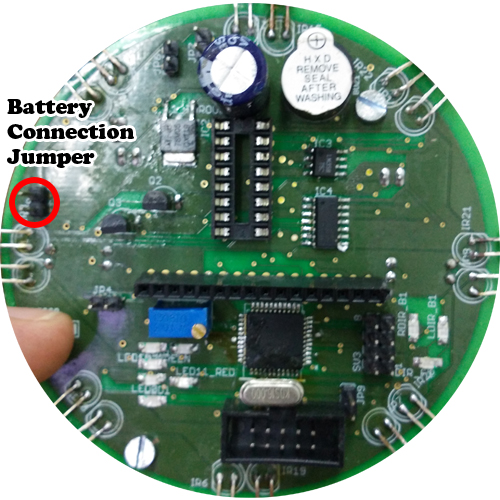
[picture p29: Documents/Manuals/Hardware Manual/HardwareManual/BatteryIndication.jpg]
	
	\caption{Battery connection jumper}
\end{figure}	
	
	\chapter[Battery Maintenance]{Battery Maintenance}
	\underline{\textbf{\Large{Battery Maintenance}}}
	\begin{itemize}
		\item {Fully charged NiMH battery will get completely discharged with in a week of storage. Always
			charge the battery before use. If fully charged battery is kept in storage for about a month and
			afterwards even if it’s fully charged again, it can deliver only 1/3rd power of its rating. In such
			case to restore battery to its full potential again, perform at least 2-3 charge discharge cycles.\\
			To ensure long life, charge battery at least once a week and discharge it till robot starts giving
			battery low warning. Before storage, charge the battery again.\\
			Disconnect the battery connector if robot is to be stored for long duration of time.}
	\end{itemize}
	
	\chapter{Motion control}
	\begin{itemize}
	\item {Mini bots has two 60 RPM DC geared motors in differential drive configuration. Robot has top speed of about 66cm per second. Using this
		configuration, the robot can turn with zero turning radius by rotating one wheel in clockwise
		direction and other in counterclockwise direction.\\
		Motion control involves direction control and velocity control. Motors are controlled by L293D
		dual motor driver which can provide up to 600mA of current to each motor. To change the
		direction of the motor, appropriate logic levels (High/Low) are applied to L293D’s direction
		control pins. Velocity control is done using Pulse Width Modulation (PWM).\\
		LEDs are connected at the input and the output stage of the motor driver for quick interpretation
		of the motion commands.}
	\end{itemize}
	\begin{figure}[h!]
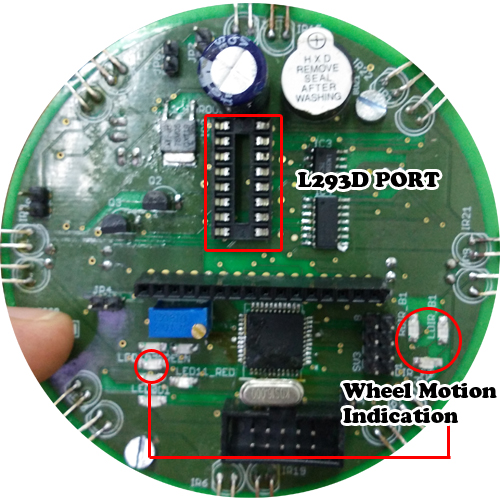
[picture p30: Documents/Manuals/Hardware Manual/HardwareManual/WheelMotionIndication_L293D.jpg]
		
		\caption{L293d port and wheel motion indication}
	\end{figure}
	\begin{figure}[h!]
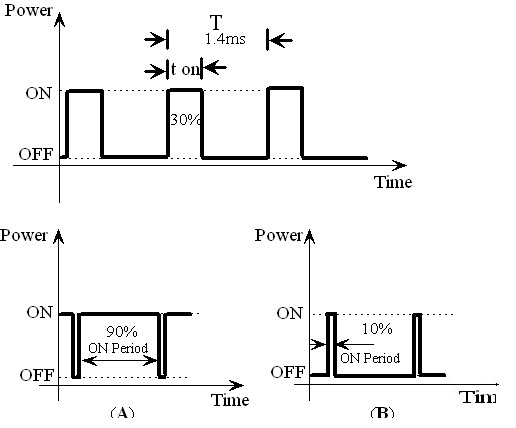
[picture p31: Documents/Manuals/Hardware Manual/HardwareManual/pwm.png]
		
		\caption{Pulse width modulation}
	\end{figure}

	\begin{itemize}
	\item {Figure 6.2 shows the PWM waveforms for motor velocity control. In case (A), ON time is 90 percent of time period. This wave has more average value. Hence more power is delivered to the
	motor. In case (B), the motor will run slower as the ON time is just 10 percent of time period.}

	\begin{tabular*}{\textwidth}{|l|c|c|}
	\hline
	- & Microcontroller pin & Function \\
	\hline
	1 & PD4 (OC1B) & Pulse width modulation for the left motor\\
	\hline
	2 & PD5 (OC1A) & Pulse width modulation for the right motor\\
	\hline
	3 & PD6 & Left motor direction control \\
	\hline
	4 & PD7 & Left motor direction control \\
	\hline
	5 & PB2 & Right motor direction control \\
	\hline
	6 & PB4 & Right motor direction control \\
	\hline
	\end{tabular*}

	\end{itemize}
	\newpage
	\hfill\\
	\begin{figure}[h!]
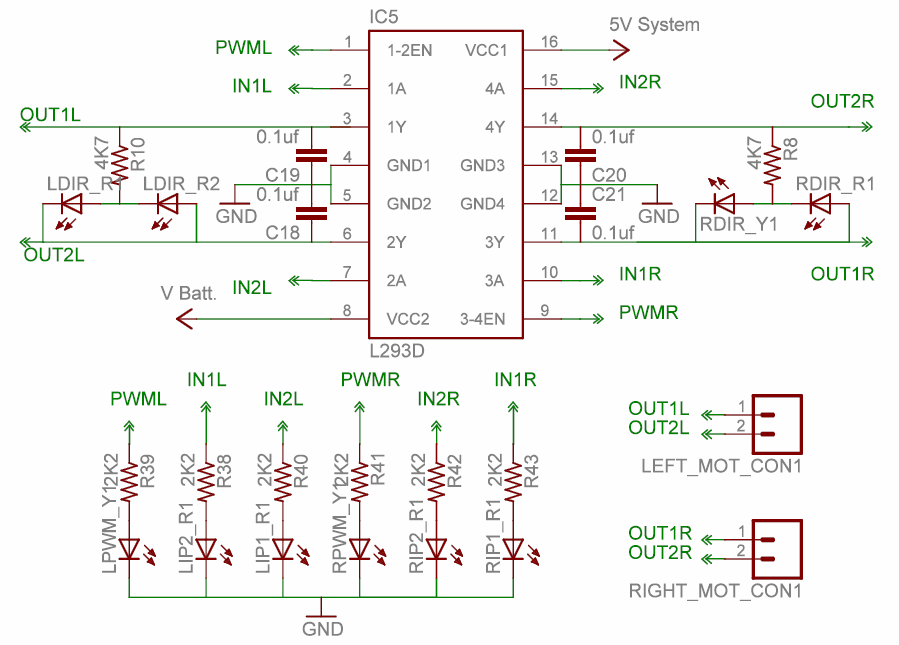
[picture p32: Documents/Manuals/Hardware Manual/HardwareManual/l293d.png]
		\centering
		\caption{Motor driver schematics}
	\end{figure}
	\hfill\\
	\chapter{Position encoders}
	\begin{itemize}
	\item {Position encoders give position / velocity feedback to the robot. It is used in closed loop to
		control robot’s position and velocity. Position encoder consists of slotted disc which rotates
		between optical encoder (optical transmitter and receiver). When slotted disc moves in between
		the optical encoder we get square wave signal whose pulse count indicates position and time
		period / frequency indicates velocity.\\
		Optical encoder MOC7811 is used for position encoder on the robot. It consists of IR LED and
		the photo transistor mounted in front of each other separated by a slot in black opaque casing
		with small slot shaped window facing each other. When IR light falls on the photo transistor it
		gets in to saturation and gives logic 0 as the output. In absence of the IR light it gives logic 1 as
		output. A slotted encoder disc is mounted on the wheel is placed in between the slot. When
		encoder disc rotates it cuts IR illumination alternately because of which photo transistor gives
		square pulse train as output. Output from the position encoder is cleaned using Schmitt trigger
		based inverter (not gate) IC CD40106. CD40106 also drives left and right position encoder status
		LEDs.
	}
	\end{itemize}

	\hfill\\
	\begin{figure}[h!]
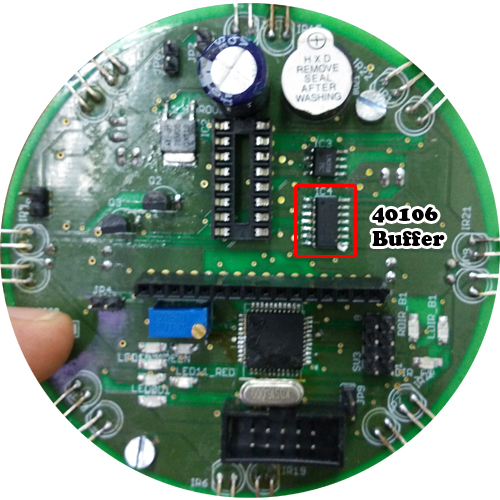
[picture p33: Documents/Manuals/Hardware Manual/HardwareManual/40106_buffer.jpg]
		
		\caption{40106 hex buffer}
	\end{figure}

	\hfill\\
	\begin{figure}[h!]
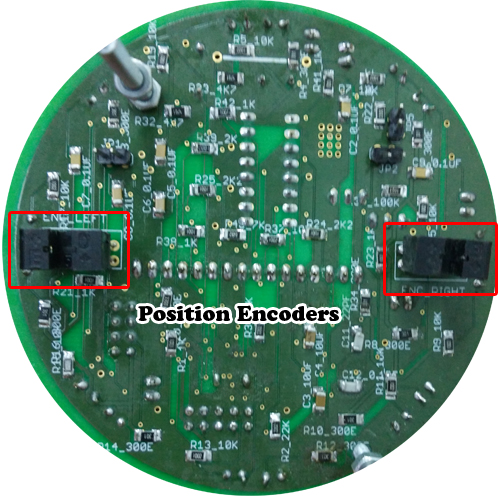
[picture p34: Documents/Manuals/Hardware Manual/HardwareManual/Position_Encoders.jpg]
		
		\caption{Position encoders}
	\end{figure}
		
	\hfill\\
	\begin{figure}[h!]
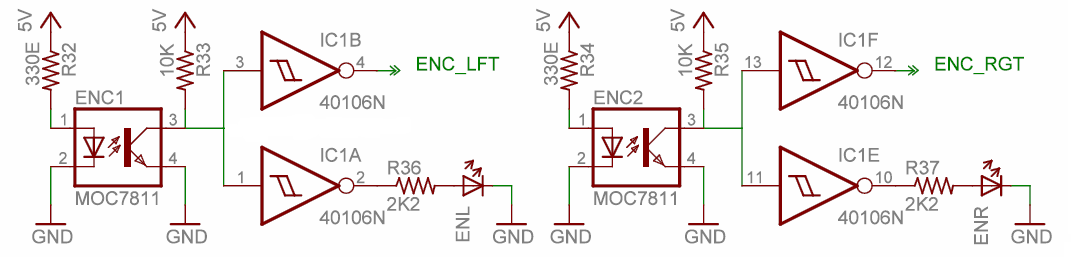
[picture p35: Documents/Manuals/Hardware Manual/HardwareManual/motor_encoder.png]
		
		\caption{Position encoders schematics}
	\end{figure}

\newpage
\hfill\\
\chapter{Infrared proximity and Directional light intensity sensors}
\begin{itemize}
	\item {
		Infrared proximity sensors are used to detect proximity of any obstacles in the short range. IR
		proximity sensors have about 10cm sensing range. Mini bots has 8 IR proximity sensors.\\
		In the absence of the obstacle there is no reflected light hence no leakage current will flow
		through the photo transistor and output voltage of the photo transistor will be around 5V. As obstacle
		comes closer, more light gets reflected and falls on the photo transistor and leakage current flowing
		through the photo transistor starts to increase which causes voltage across the diode to fall.\\
		If IR LEDs are disabled using jumpers then same photo transistors works as directional light
		intensity sensors.
		IR sensors detect the light from the transmitters present on the neighbouring robots for determining direction and distance of robots.\\
	}
	\end{itemize}

	\hfill\\
	\begin{figure}[h!]
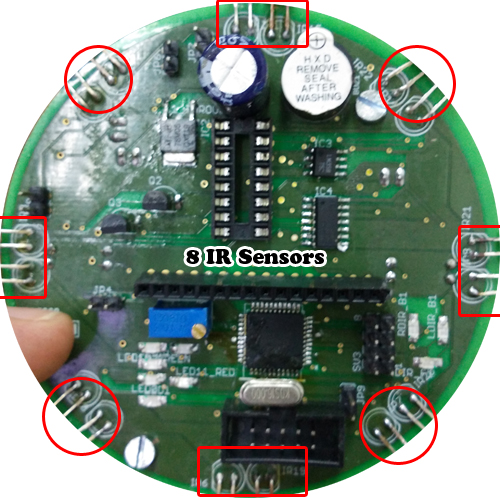
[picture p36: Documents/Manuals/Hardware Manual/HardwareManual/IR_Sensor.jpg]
		
		\caption{IR sensors}
	\end{figure}	
	\hfill\\
	\newpage
	\underline{\textbf{\Large{LCD}}}
		
	\hfill\\
	\begin{figure}[h!]
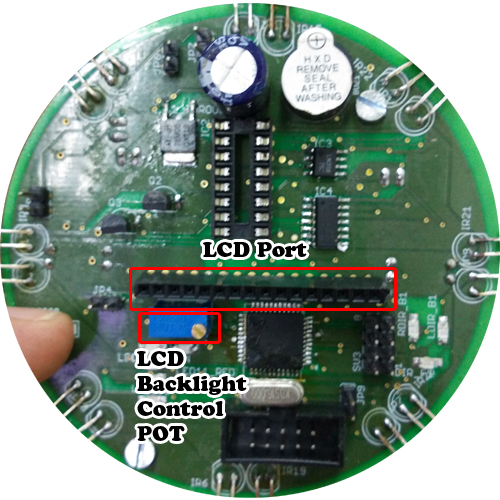
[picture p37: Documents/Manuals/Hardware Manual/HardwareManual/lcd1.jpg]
		
		\caption{LCD port}
	\end{figure}	
	\hfill\\
	
	\begin{itemize}
	\item {
	To interface LCD with the microcontroller in default configuration requires 3 control signals and
	8 data lines. This is known as 8 bit interfacing mode which requires total 11 I/O lines. To reduce
	the number of I/Os required for LCD interfacing we can use 4 bit interfacing mode which
	requires 3 control signals with 4 data lines. In this mode higher nibble and lower nibble of
	commands/data set needs to be sent separately.LCD is interfaced in 4 bit
	mode. The three control lines are referred to as EN, RS, and RW.
	}
	\end{itemize}

	\hfill\\
	\begin{figure}[h!]
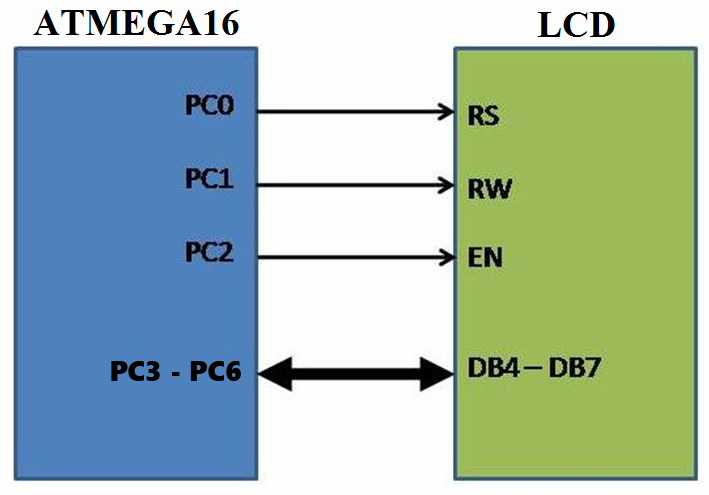
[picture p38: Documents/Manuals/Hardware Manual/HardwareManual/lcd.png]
		
		\caption{Block diagram of lcd connection to atmega16}
	\end{figure}	
	\hfill\\
	
	\begin{itemize}
	\item {
		The EN line is called "Enable". This control line is used to tell the
		LCD that microcontroller has sent data to it or microcontroller is ready to receive data from
		LCD. This is indicated by a high-to-low transition on this line. To send data to the LCD, program
		should make sure that this line is low (0) and then set the other two control lines as required and
		put data on the data bus. When this is done, make EN high (1) and wait for the minimum amount
		of time as specified by the LCD datasheet, and end by bringing it to low (0) again.\\
		The RS line is the "Register Select" line and it is connected to PC0. When RS is low (0), the data
		is treated as a command or special instruction by the LCD (such as clear screen, position cursor,
		etc.). When RS is high (1), the data being sent is treated as text data which should be displayed
		on the screen.\\
		The RW line is the "Read/Write" control line. When RW is low (0),
		the information on the data bus is being written to the LCD. When RW is high (1), the program
		is effectively querying (or reading from) the LCD.\\
		The data bus is bidirectional, 4 bit wide.
		The MSB bit of data bus is also used as a Busy flag. When the Busy flag is 1, the LCD is
		in internal operation mode, and the next instruction will not be accepted. When RS = 0 and R/W
		= 1, the Busy flag is output. The next instruction must be written after ensuring that the
		busy flag is 0.
	}
	\end{itemize}

	\hfill\\
	\begin{figure}[h!]
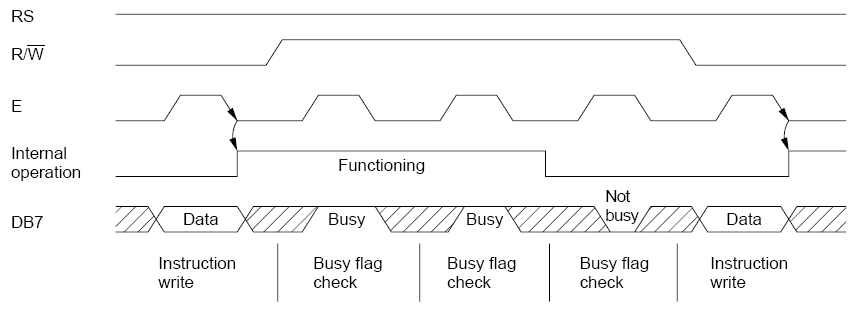
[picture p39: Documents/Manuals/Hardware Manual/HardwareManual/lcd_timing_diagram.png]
		
		\caption{Timing diagram for lcd}
	\end{figure}	
	\hfill\\
	\newpage
	
	\chapter[LCD contrast and backlight setting]{LCD contrast and backlight setting}
	\underline{\textbf{\Large{LCD contrast and backlight setting}}}
	\begin{itemize}
	\item{Contrast of the LCD can be adjusted by adjusting the potentiometer. To save power its backlight can also be turned off by removing jumper.}
	\end{itemize}
	
	\hfill\\
	\begin{figure}[h!]
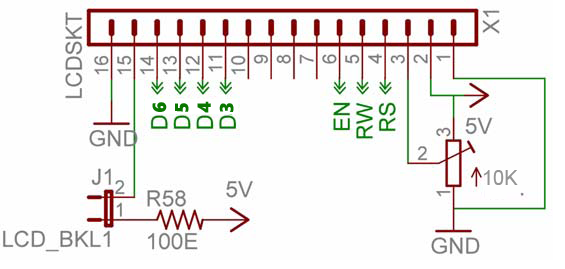
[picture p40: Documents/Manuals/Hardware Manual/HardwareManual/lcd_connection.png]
		
		\caption{Schematics of Lcd connection}
	\end{figure}	
	\hfill\\
	\newpage
	
	\chapter[Battery voltage sensor]{Battery voltage sensor}
	\underline{\textbf{\Large{Battery voltage sensor}}}
	\begin{itemize}
		\item{Two registers of 22K ohms are used to scale down the battery voltage below 5V and given to the
			comparator circuit. Voltage divider network of these register will give half of the
			battery voltage.}
	\end{itemize}

	\hfill\\
	\begin{figure}[h!]
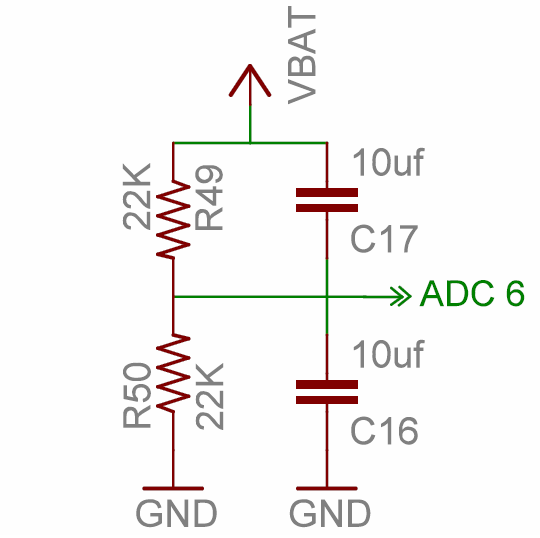
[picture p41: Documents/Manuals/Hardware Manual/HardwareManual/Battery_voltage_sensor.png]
		
		\caption{Battery sensing circuit}
	\end{figure}	
	
	\chapter[Atmega 16 programmer]{Atmega 16 programmer}
	\underline{\textbf{\Large{Atmega 16 programmer}}}
	
	\hfill\\
	\begin{figure}[h!]
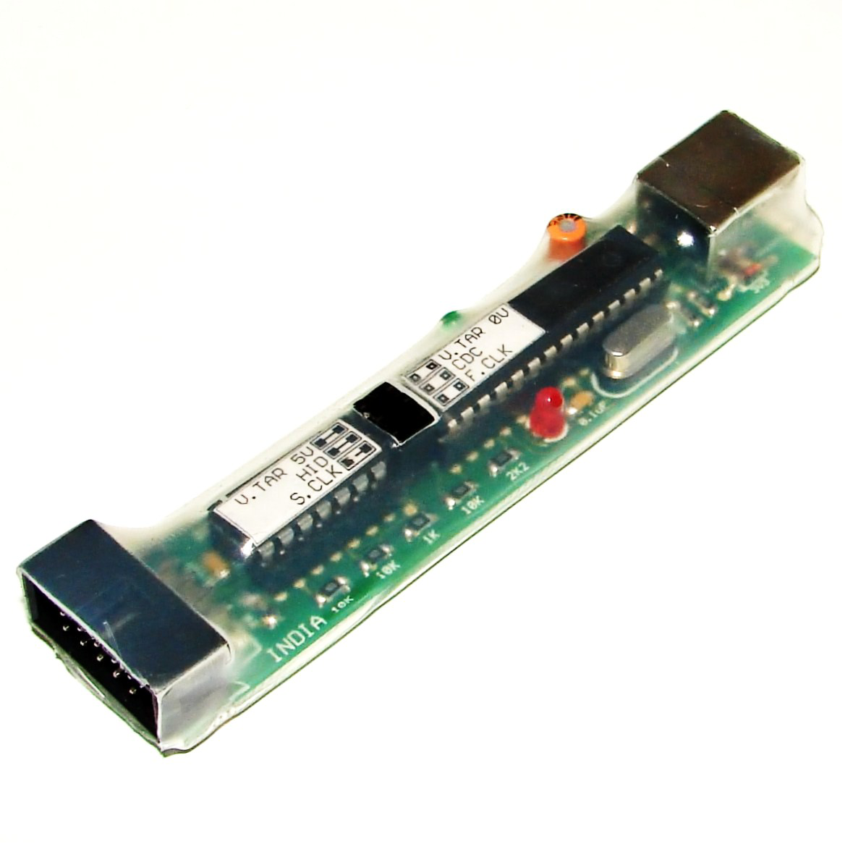
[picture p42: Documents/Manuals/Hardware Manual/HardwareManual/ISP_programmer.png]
		\centering
		\caption{ISP programmer}
	\end{figure}	
	\hfill\\
	
	\begin{itemize}
	\item{Mini bots have ATMEGA16 microcontroller running at 16MHz. Robot is programmed by ISP (In System Programming) using AVR USB programmer from NEX
		Robotics or ATMEL’s AVR ISP mkII.}
	\end{itemize}
	
	\chapter[Schematics]{Schematics}
	\underline{\textbf{\Large{Schematics}}}
	\begin{figure}[h!]
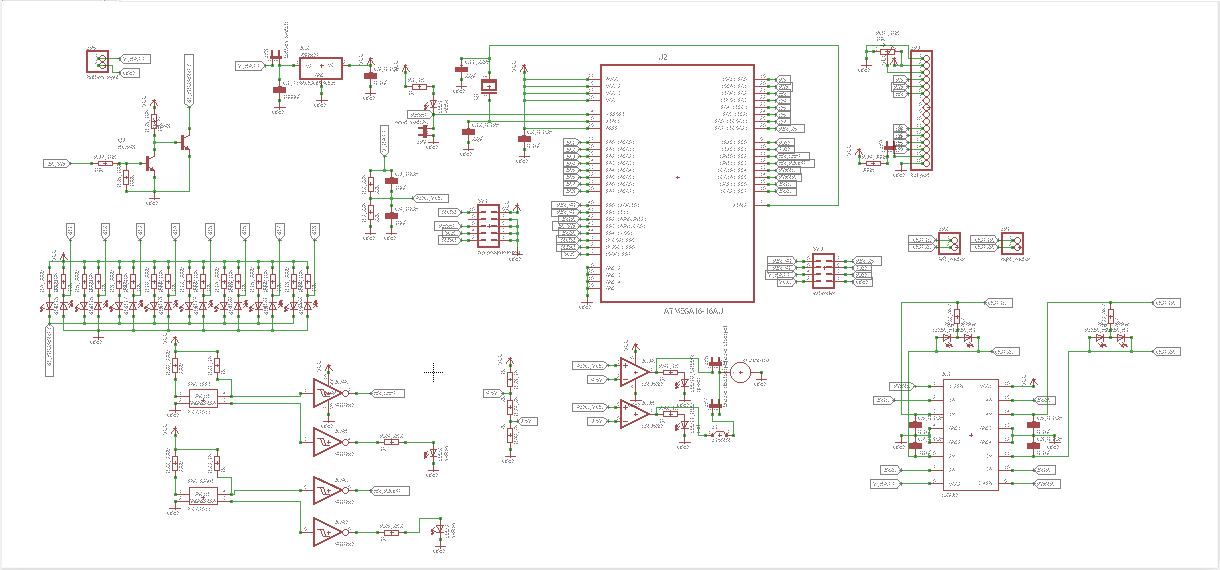
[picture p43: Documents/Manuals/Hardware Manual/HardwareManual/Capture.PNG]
		
		\caption{Complete schematic of pcb}
	\end{figure}	
	
	\chapter[Layout]{Layout}
	\underline{\textbf{\Large{Layout}}}

	\begin{figure}[h!]
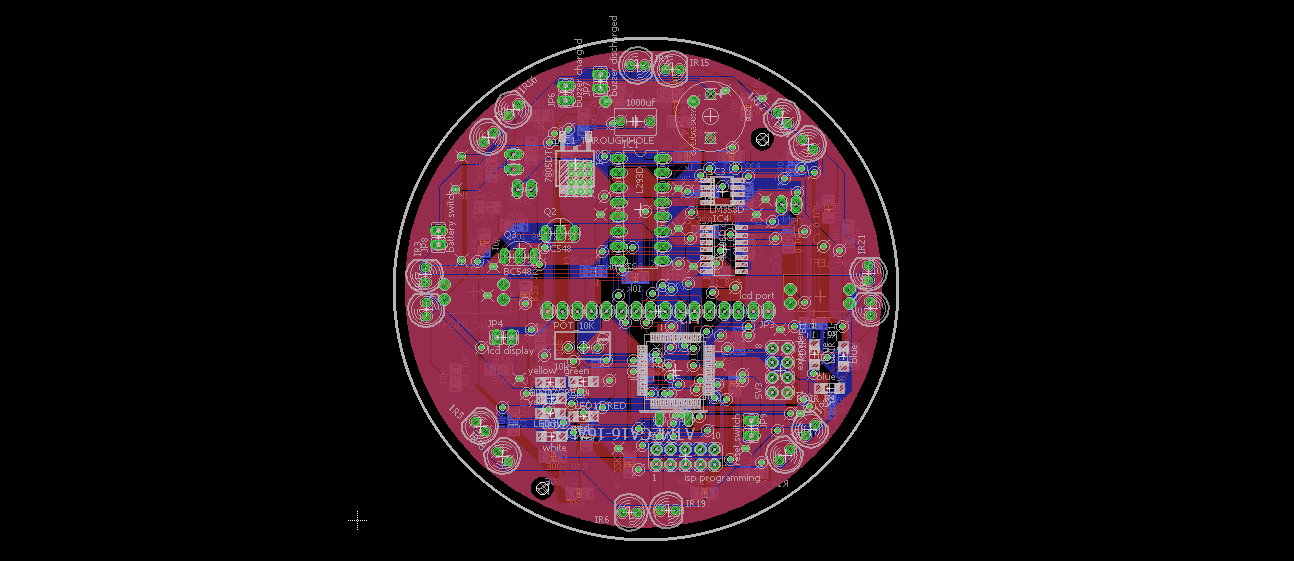
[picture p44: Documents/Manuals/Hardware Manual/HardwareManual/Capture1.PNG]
		
		\caption{Complete layout of pcb}
	\end{figure}		

\begin{tabular*}{\textwidth}{|l|c|c|}
	\hline
	SR NO & PIN NAME & USED FOR \\
	\hline
	1 & (XCO/T0)PB0 & Expansion pin\\
	\hline
	2 & (T1)PB1 & Expansion pin\\
	\hline
	3 & (INT2/AIN0)PB2 & Logic output 1 for Left motor\\
	\hline
	4 & (OC0/AIN1)PB3 & IR switch \\
	\hline
	5 & (SS)PB4 & ISP (In System Programming) \\
	\hline
	6 & (MOSI)PB5 & ISP (In System Programming) \\
	\hline
	7 & (MISO)PB6 & ISP (In System Programming) \\
	\hline
	8 & (SCK)PB7 & ISP (In System Programming) \\
	\hline
	9 & RESET & Microcontroller reset \\
	\hline
	10 & VCC & 5V \\
	\hline
	11 & GND & Ground \\
	\hline
	12 & XTAL1 & Crystal 16 MHz \\
	\hline
	13 & XTAL2 & Crystal 16 MHz \\
	\hline
	14 & (RXD)PD0 & UART Receive* \\
	\hline
	15 & (TXD)PD1 & UART Transmit* \\
	\hline
	16 & (INT0)PD2 & Position Encoder input for Left Motor \\
	\hline
	17 & (INT1)PD3 & Position Encoder input for Right Motor \\
	\hline
	18 & (OC1B)PD4 & PWM output for Left Motor \\
	\hline
	19 & (OC1A)PD5 & PWM output for Right Motor  \\
	\hline
	20 & (ICP1)PD6 & Logic output 1 for Left motor \\
	\hline
	21 & (OC2)PD7 & Logic output 1 for Left motor \\
	\hline
	22 & PC0(SCL) & LCD control line RS (Register Select) \\
	\hline
	23 & PC1(SDA) & LCD control line RW(Read/Write Select) \\
	\hline
	24 & PC2(TCK) & LCD control line EN(Enable Signal) \\
	\hline
	25 & PC3(TMS) & LCD data lines (4-bit mode) \\
	\hline
	26 & PC4(TDO) & LCD data lines (4-bit mode) \\
	\hline
	27 & PC5(TDI) & LCD data lines (4-bit mode) \\
	\hline
	28 & PC6(TOSC1) & LCD data lines (4-bit mode) \\
	\hline
	29 & PC7(TOSC2) & Expansion pin \\
	\hline
	30 & AVCC & 5V \\
	\hline
	31 & AGND & Ground \\
	\hline
	32 & AREF & ADC reference voltage pin (5V external) \\
	\hline
	33 & PA7 (ADC7) & ADC input for analog IR proximity sensor\\
	\hline
	34 & PA6(ADC6) & ADC input for analog IR proximity sensor\\
	\hline
	35 & PA5(ADC5) & ADC input for analog IR proximity sensor\\
	\hline
	36 & PA4(ADC4) & ADC input for analog IR proximity sensor\\
	\hline
	37 & PA3(ADC3) & ADC input for analog IR proximity sensor\\
	\hline
	38 & PA2(ADC2) & ADC input for analog IR proximity sensor\\
	\hline
	39 & PA1(ADC1) & ADC input for analog IR proximity sensor\\
	\hline
	40 & PA0(ADC0) & ADC input for analog IR proximity sensor\\
	\hline
\end{tabular*}

\end{document}

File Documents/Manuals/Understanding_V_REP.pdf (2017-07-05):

### Understanding V-REP simulator

Author: R Hariharan
Introduction

V-REP simulator is used to analyse the working of your robot. We used V-REP to simulate the “Circle formation algorithm” and the “Generic shape formation algorithm”. We found V-REP to be an easier simulator to use, compared other simulators like gazebo. V-REP provides the user with an easy to use GUI and different API’s for the convenience of the user. This document just gives a brief idea of V-REP, to know more go to V-REP official website. (http://www.coppeliarobotics.com/resources.html)
Installation/Download

V-REP is available for Ubuntu, Mac and Windows. We used V-REP in Ubuntu 16.04
platform. | Here’s | a | link | to | download | V-REP | @
http://www.coppeliarobotics.com/downloads.html. | The | Educational | licence
provides all features of V-REP.
After downloading V-REP for ubuntu, navigate to that folder and then open your terminal in that folder itself. Type ./vrep.sh to run the simulator.
In case you are using Mac or Windows check out the V-REP forum (http://www.forum.coppeliarobotics.com/index.php) for help.
GUI of the Simulator

When you run the simulator you can see that it has multiple windows open. One of them is the scene window which consist the scene hierarchy, this is where you models will be shown. There is model browser which shows all the available robots that are present in V-REP (check out the mobile robots present in the robot). Simulation window is where the models in the scene are show.
The simulator has a menu bar which gives access to all the available tools in the simulator. The tool bar gives clickable icons, to control the simulation environment (move objects around, rotate the objects, zoom in/out of the simulation window, move the simulation window around, rotate the view of the simulation window etc).
The tool bar also has the simulation tools, which allows the user to start, pause and stop the simulation. It has dropdown menus where you can set the physics engine you want to use and the time interval to run each simulation cycle. There are two button with icons as tortoise and rabbit to decrease and increase the simulation speed repectively.
For detailed explanation visit the User Interfaces section of the V-REP User Manual. (http://www.coppeliarobotics.com/helpFiles/)
Models and Collections

Scenes have objects like cameras, shapes, sensors etc. These objects are nothing but models. So a robot has multiple models attached to it. A collection is a set of models. So a robot is not a model but a collection. In order to work with a robot we need to define it has a collection.

For detailed explanation visit the Scenes and Models section of the V-REP User Manual. (http://www.coppeliarobotics.com/helpFiles/)
Writing Code

Any user can program into V-REP using these ways, 1) Embedded Scripts, 2) Plugins, 3) Remote API, 4) Add on’s and 5) ROS node.
I used embedded scripts to program my robot. Embedded scripts are written in a programming language called lua. (http://www.coppeliarobotics.com/helpFiles/en/luaCrashCourse.htm)
There are two types of embedded scripts, Main script (http://www.coppeliarobotics.com/helpFiles/en/mainScript.htm) – which takes care of initializing the simulator environment and running all the child scripts. Second is the Child Scripts (http://www.coppeliarobotics.com/helpFiles/en/childScripts.htm) which is embedded with are mobile/non-mobile robots. Do not change or edit the Main Script. The script is shown as a page beside the name of the model in the scene hierarchy. Double clicking on the icon opens the script in a text editor of lua. The Child Scripts are further divided into threaded and non-threaded scripts. To get a better knowledge about the threaded and
non-threaded | child | scripts | visit
http://www.coppeliarobotics.com/helpFiles/en/childScript.htm.
The embedded scripts use the regular API’s. (http://www.coppeliarobotics.com/helpFiles/en/apiOverview.htm)
To know more about other means of coding visit the Writing code in and around V-REP section of the V-REP User Manual. (http://www.coppeliarobotics.com/helpFiles/)
Functioning of the Simulator

To run the simulator we should click the play button, we can set the simulation speed and the physics engine from the drop down menu. When the simulation starts it runs all the embedded scripts parallely. The embedded scripts runs in this fashion, first it runs the intialisation part of the child script once then it run the actuation part and the sensing part in a loop. When the simulation is stopped the cleanup part of the code is run.
This cycle keeps happening based on the simulation time interval you have set, hence you can’t run loops (while or for loops) which runs for more then the time interval set.
Remeber this is only for embedded child scripts. To know more about other means of coding visit the Writing code in and around V-REP section of the V-REP User Manual. (http://www.coppeliarobotics.com/helpFiles/)
Building your own model

V-REP User Manual (http://www.coppeliarobotics.com/helpFiles/) has a tutorials section. In this section the first tutorial is to build a bubbleRobot. Doing this tutorial will help in understanding the V-REP simulator better. After completion of this tutorial, any user will be able to use the simulator easily. This tutorial explains how to create shapes, add sensors to it, change sensor variable like range of the sensor, placing of the sensors (positioning) and even orientation, adding scripts to the robot, making a collection of the robot etc. This tutorial is really helpfull.

References

1) To understand the simulator to its depth read the V-REP User Manual. (http://www.coppeliarobotics.com/helpFiles/)
2) If you have any question visit the V-REP Forum. (http://www.forum.coppeliarobotics.com/)
3) List of all regular API functions. (http://www.coppeliarobotics.com/helpFiles/en/apiFunctionListCategory.htm)

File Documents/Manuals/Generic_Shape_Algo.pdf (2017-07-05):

## Generic Shape Formation Algorithm for a System of Distributed Robots

Chinmay C (2

nd year ECE, RV College of Engineering, Bangalore) R Hariharan (3

rd year CSE, PES University, Bangalore) Mentors:
Ms. Rutuja (ERTS Lab, IIT Bombay, Mumbai) Ms. Deepa (ERTS Lab, IIT Bombay, Mumbai)

Abstract:

In swarm robotics one of the swarm behaviours is to form patterns and shapes. The algorithm that we are proposing has the capability to form some regular shapes, alphabets and even numbers. The algorithm defines shapes as defined in a 14 segment display. Based on this input each individual robot finds its corresponding position in shape the user desires.

INPUT:

Each shape is defined by a 14 segment display

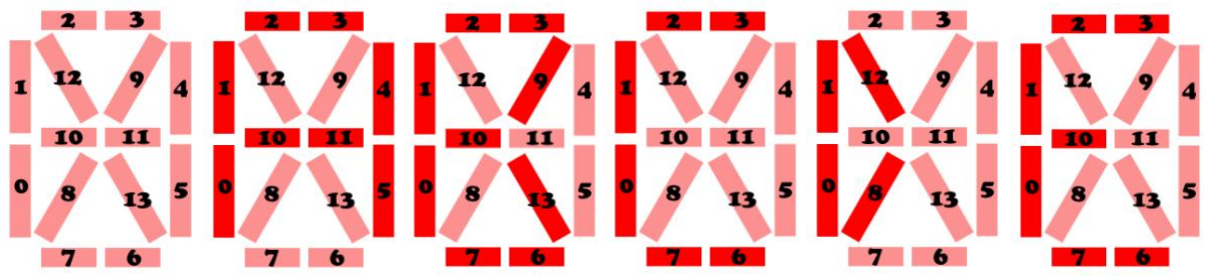
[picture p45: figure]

Fig 1. Figure represent shapes A, B, C, D & E formed from the 14 segment display
The 14 segment display can understood like a Boolean array of size 14 (indexes represented in the figure). True representing the segment is ON, False representing segment in OFF. The segments are represented as a pair of vertices. Each vertex is a co-ordinate in a global co-ordinate system. The intersection of segments ‘0’ and ‘7’ is the origin and segment ‘0’ lies on the positive y-axis. With respect to this co-ordinate system and the scale factor the other vertex co-ordinates are established. The scale factor is used to define the number of robots preset to make the shape. To make the shape scalable we can change this variable. So, the input to the algorithm is the shape information as Boolean array of size 14 and the co-ordinates of all the vertices.

Algorithm:

We now know that shapes are represented as segments and segments have vertices. So, in our algorithm the robots fill these vertices. The points the robots fill can be broadly classified as Main vertices, Fill/Secondary vertices and Fill Edge points (Represented as green boxes, blue boxes and white circles in figure 2). The main vertices are the minimum number of vertices to be filled such that the shape can be represented. The fill/secondary vertices are the next order vertices which are filled to represent the shape better after all the main vertices are filled. The fill edge points are filled after by the extra robots which do not have place in either main vertices or fill/secondary vertices. So, the order of filling the shape is Main vertices – Fill/Secondary vertices – Fill edge points.

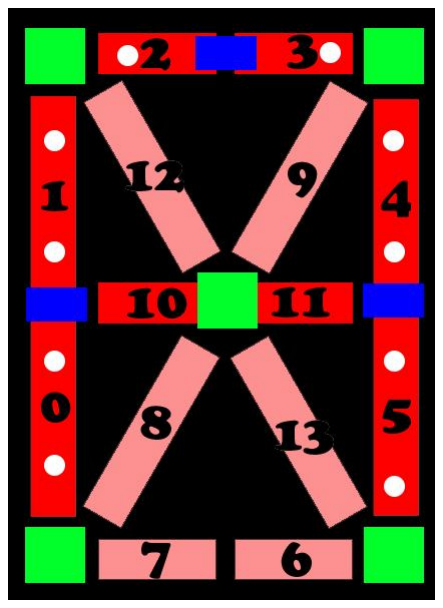
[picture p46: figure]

Fig 2. Shape ‘A’ which shows Main Vertices (Green Boxes), Fill/Secondary vertices (Blue Boxes), Fill Edge points (White circles)
With this hierarchy established, the algorithm first generates the main vertices, fill/secondary vertices and the fill edge points. The robots get their position w.r.t the global co-ordinate system and moves to the nearest main vertex. If the main vertex is filled by another robot then it moves to the next nearest main vertex, this loop runs until it finds a free main vertex or all main vertices are filled. If the main vertices are filled then the robot tries to fill the fill/secondary vertices. If both the main and secondary vertices are filled then the robot fills the fill edge points. If there is no spot available for the robot, it moves out of the shape. The method used to check if the nearest vertex is available or not is based on the robot model. In our implementation of the algorithm, the robot went to each vertex and checked if the spot is available or not, using IR proximity sensor. Other ways of finding out the same may be to use some kind of a communication system (ZigBee).

The flow chart is available in the Appendix.

Complications in algorithm:

The algorithm depends on two factors, 1) while moving to a vertex, how avoid other robots? And 2) when multiple robots are approaching the same vertex, how to break the tie? These can itself be researched to find the best algorithm that we can use. So choosing the best algorithm for the both improves the efficiency of our algorithm.

Future Improvements:

The algorithm as of now is not scalable, as in the number of robots that can fill the shape is fixed and the extra robots must leave the shape. Hence one of the improvements that can be made is to make the shape dynamically scalable. One of the ways to do it is by increasing the number of fill edge points, by increasing the scale factor dynamically. Scale factor determines the vertices of all the segments, so changing it dynamically can scale the size. But the challenge here is to make all the distributed robots agree upon the new scale factor. Another improvement is to make the algorithm work in a relative co-ordinate system environment. Each robot now has its own perspective of the co-ordinate system.

Conclusion:

The proposed algorithm will form some regular shapes (triangle, rectangle & square), all alphabets and all digits. We can even increase the number of segments to show more shapes. When the number of robots forming the shape is less the shape is formed fast, but the shape cannot be purely identified. As the number of robots increase the two factors we talked about earlier starts to dominate and the time taken to form the shape reduces. So, finding the best dynamic robot avoidance algorithm and tie breaking algorithm for distributed robots plays a crucial role.

Appendix:

Link to the implantation code in V-REP simulation - https://github.com/eYSIP-2017/eYSIP-2017_DistributedRobotics/tree/master/Codes/2017-7-05/V-REP (https://github.com/eYSIP-2017/eYSIP-2017_DistributedRobotics/tree/master/Codes/2017-7-05/V-REP)

Flow Chart

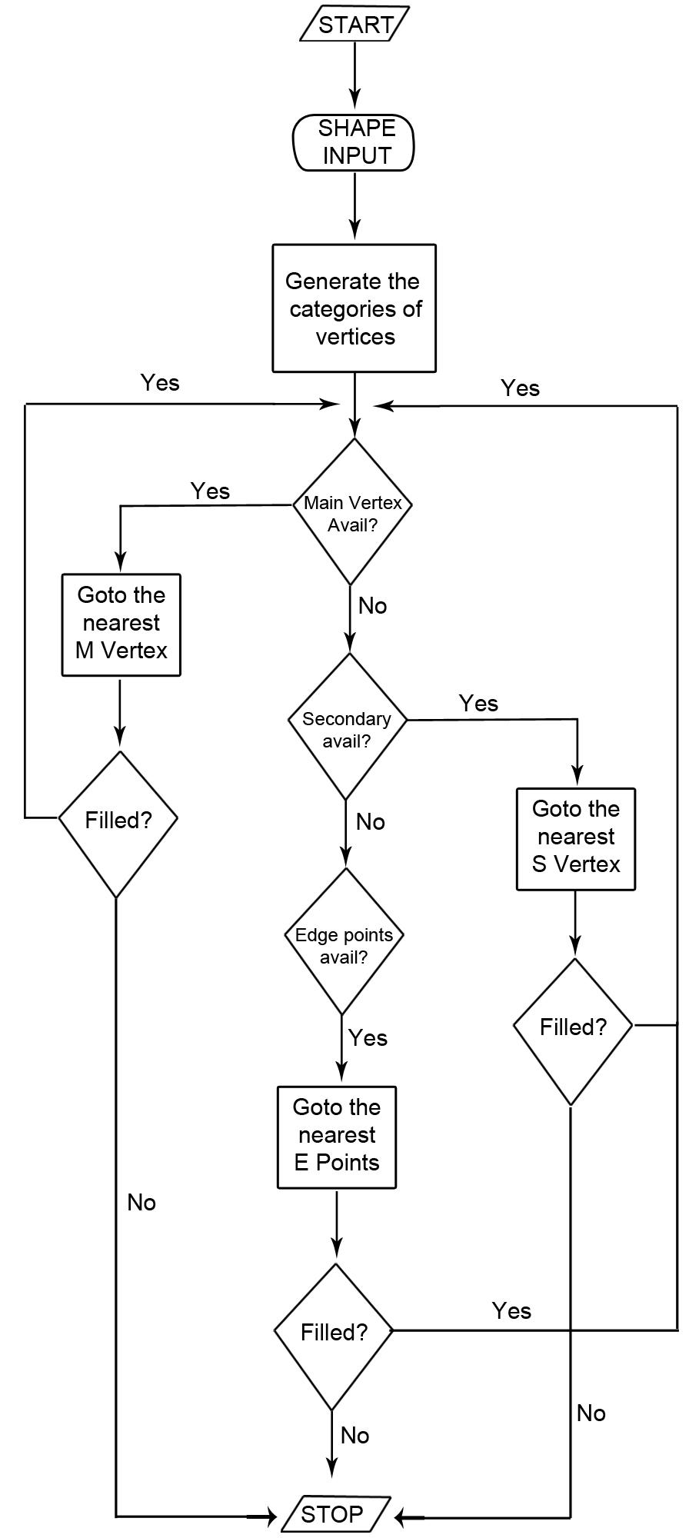
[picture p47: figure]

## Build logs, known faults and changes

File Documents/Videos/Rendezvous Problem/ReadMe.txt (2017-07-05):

These Videos show the Rendezvous of two robots without communicating with each other, but by only sensing the surrounding for any other robots and going to the centroid of the shape formed by these robots. (AKA Rendezvous Problem)

Platform : Firebird V (Nex Robotics)
For further reference : https://github.com/akshar100/eyantra-firebird-resources/tree/master/Fire%20Bird%20V%20ATMEGA2560%20Robots%202010-12-29

Code for the same can be found @ https://github.com/eYSIP-2017/eYSIP-2017_DistributedRobotics/tree/master/Codes/2017-5-31/20170530_1452_RandevousProblem

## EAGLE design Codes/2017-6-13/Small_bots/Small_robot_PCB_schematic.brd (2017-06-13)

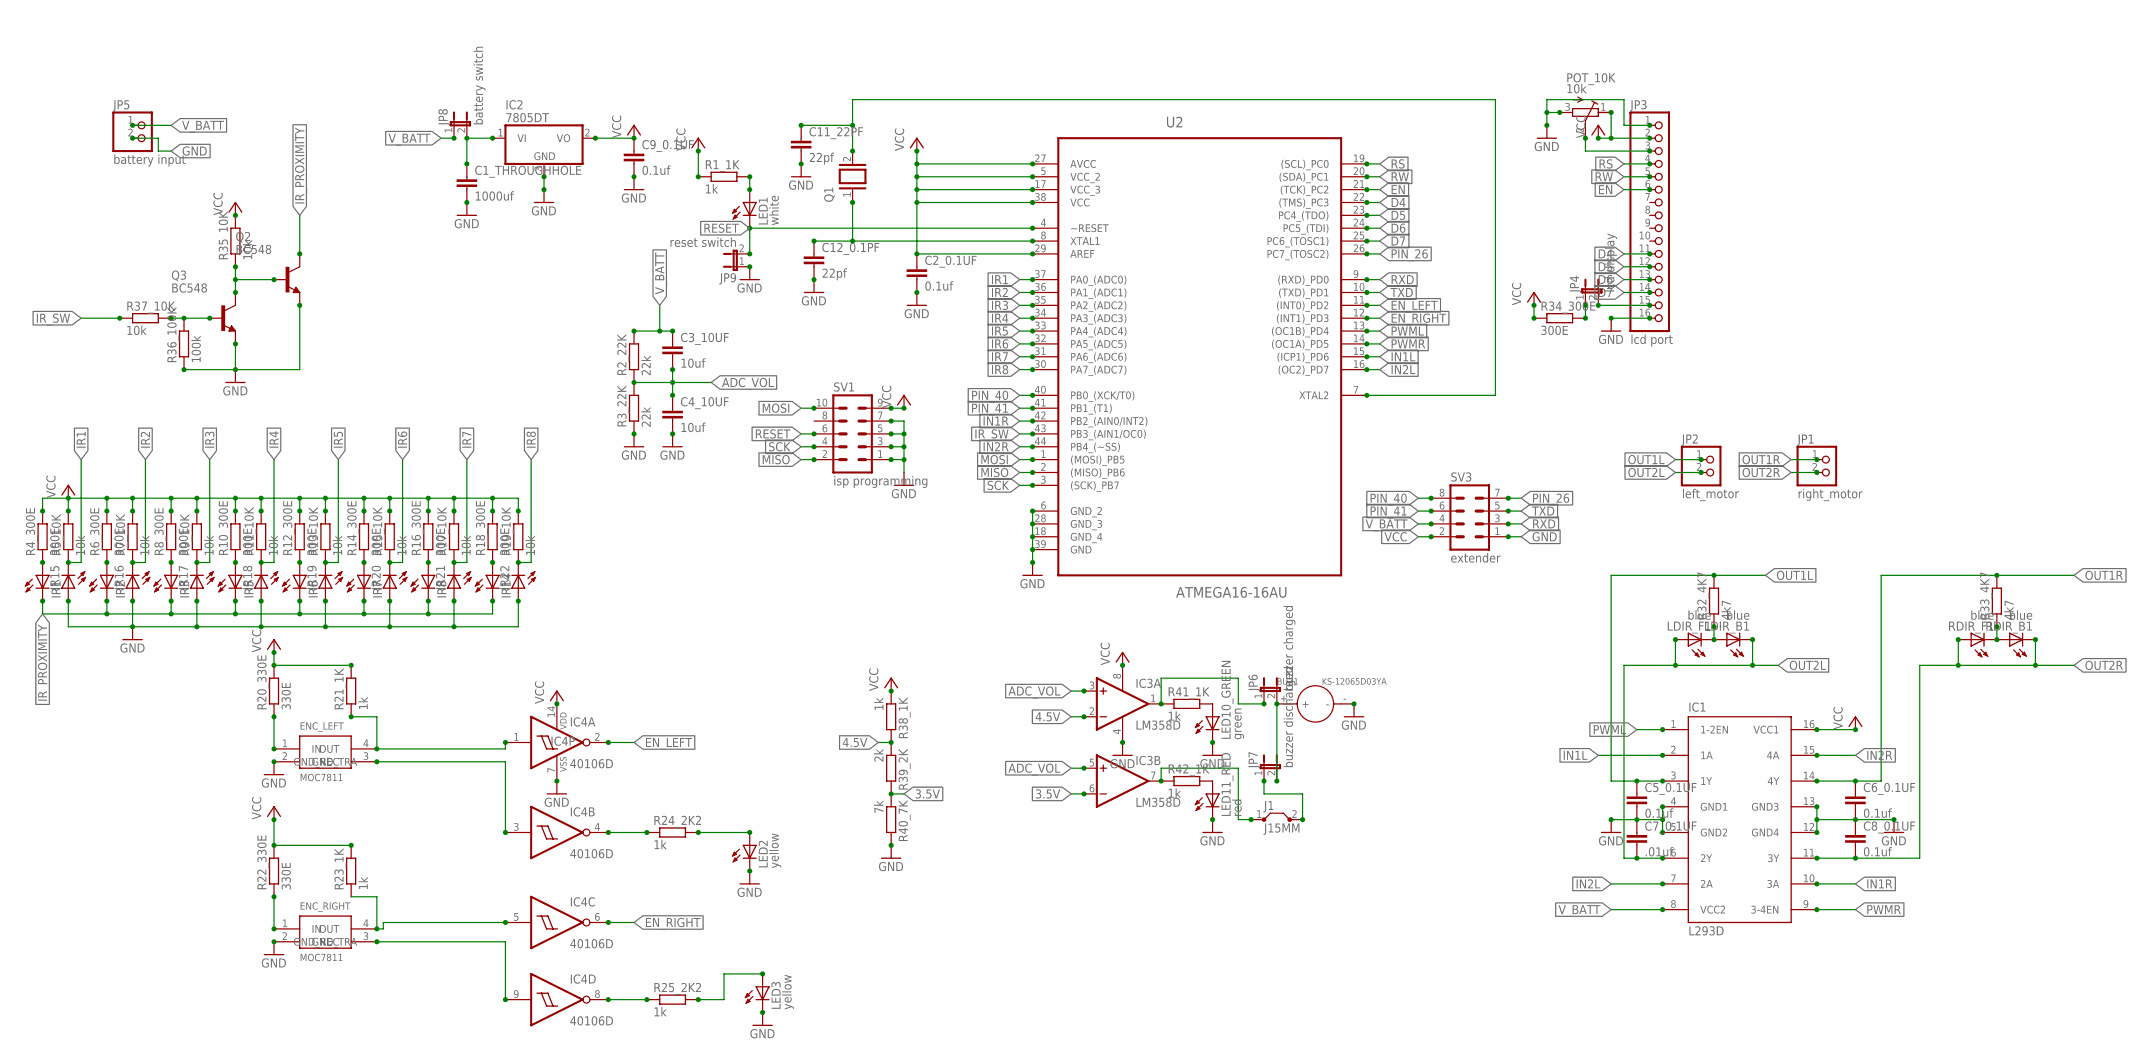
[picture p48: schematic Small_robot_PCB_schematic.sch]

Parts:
BUZ1: KS-12065D03YA; BZ2-7.6-D12.0XH6.5MM
C1_THROUGHHOLE: 1000uf; C050-045X075
C2_0.1UF, C5_0.1UF, C6_0.1UF, C8_0.1UF, C9_0.1UF: 0.1uf; C1206
C3_10UF, C4_10UF: 10uf; C1206
C7_0.1UF: .01uf; C1206
C11_22PF, C12_0.1PF: 22pf; C1206
ENC_LEFT: MOC7811; THROUGH_HOLE_NORMAL
ENC_RIGHT: MOC7811; THROUGH_HOLE_NORMAL
IC1: L293D; DIL16
IC2: 7805DT; TO252
IC3: LM358D; SO08
IC4: 40106D; SO14
IR1, IR2, IR3, IR5, IR6, IR7, IR8, IR14, IR15, IR16, IR17, IR18, IR19, IR20, IR21, IR22: LED5MM
J1: J15MM; 15
JP1: right_motor; 1X02
JP2: left_motor; 1X02
JP3: lcd port; 1X16
JP4: lcd display; JP1
JP5: battery input; 1X02
JP6: buzzer charged; JP1
JP7: buzzer discharged; JP1
JP8: battery switch; JP1
JP9: reset switch; JP1
LDIR_B1: blue; CHIPLED_1206
LDIR_F1: blue; CHIPLED_1206
LED1: white; CHIPLED_1206
LED2, LED3: yellow; CHIPLED_1206
LED10_GREEN: green; CHIPLED_1206
LED11_RED: red; CHIPLED_1206
POT_10K: 10k; RTRIMT93YA
Q1: XTAL; Q
Q2, Q3: BC548; TO92-EBC
R1_1K, R21_1K, R23_1K, R24_2K2, R25_2K2, R38_1K, R41_1K, R42_1K: 1k; R1206
R2_22K, R3_22K: 22k; R1206
R4_300E, R6_300E, R8_300E, R10_300E, R12_300E, R14_300E, R16_300E, R18_300E, R34_300E: 300E; R1206
R5_10K, R7_10K, R9_10K, R11_10K, R13_10K, R15_10K, R17_10K, R19_10K, R35_10K, R37_10K: 10k; R1206
R20_330E, R22_330E: 330E; R1206
R32_4K7, R33_4K7: 4k7; R1206
R36_100K: 100k; R1206
R39_2K: 2k; R1206
R40_7K: 7k; R1206
RDIR_B1: blue; CHIPLED_1206
RDIR_F1: blue; CHIPLED_1206
SV1: isp programming; MA05-2
SV3: extender; MA04-2
U2: ATMEGA16-16AU; QFP80P1200X1200X120-44N

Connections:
3.5V: IC3.6 (-IN), R39_2K.2, R40_7K.1
4.5V: IC3.2 (-IN), R38_1K.2, R39_2K.1
ADC_VOL: C3_10UF.2, C4_10UF.1, IC3.3 (+IN), IC3.5 (+IN), R2_22K.1, R3_22K.2
D4: JP3.11, U2.22 ((TMS)_PC3)
D5: JP3.12, U2.23 (PC4_(TDO))
D6: JP3.13, U2.24 (PC5_(TDI))
D7: JP3.14, U2.25 (PC6_(TOSC1))
EN: JP3.6, U2.21 ((TCK)_PC2)
EN_LEFT: IC4.2 (O), U2.11 ((INT0)_PD2)
EN_RIGHT: IC4.6 (O), U2.12 ((INT1)_PD3)
GND: BUZ1.-, C1_THROUGHHOLE.2, C2_0.1UF.2, C4_10UF.2, C5_0.1UF.2, C6_0.1UF.2, C7_0.1UF.1, C8_0.1UF.1, C9_0.1UF.2, C11_22PF.2, C12_0.1PF.2, ENC_LEFT.2 (GND_TRA), ENC_RIGHT.2 (GND_TRA), IC1.4 (GND1), IC1.5 (GND2), IC1.12 (GND4), IC1.13 (GND3), IC2.3 (GND), IC3.4 (V-), IC4.7 (VSS), IR15.A, IR16.A, IR17.A, IR18.A, IR19.A, IR20.A, IR21.A, IR22.A, JP3.1, JP3.16, JP5.2, JP9.1, LED2.C, LED3.C, LED10_GREEN.C, LED11_RED.C, POT_10K.3 (A), Q2.E, Q3.E, R3_22K.1, R36_100K.1, R40_7K.2, SV1.1, SV1.3, SV1.5, SV1.7, SV3.1, U2.6 (GND_2), U2.18 (GND_4), U2.28 (GND_3), U2.39 (GND)
IN1L: IC1.2 (1A), U2.15 ((ICP1)_PD6)
IN1R: IC1.10 (3A), U2.42 (PB2_(AIN0/INT2))
IN2L: IC1.7 (2A), U2.16 ((OC2)_PD7)
IN2R: IC1.15 (4A), U2.44 (PB4_(~SS))
IR1: IR15.K (C), R5_10K.1, U2.37 (PA0_(ADC0))
IR2: IR16.K (C), R7_10K.1, U2.36 (PA1_(ADC1))
IR3: IR17.K (C), R9_10K.1, U2.35 (PA2_(ADC2))
IR4: IR18.K (C), R11_10K.1, U2.34 (PA3_(ADC3))
IR5: IR19.K (C), R13_10K.1, U2.33 (PA4_(ADC4))
IR6: IR20.K (C), R15_10K.1, U2.32 (PA5_(ADC5))
IR7: IR21.K (C), R17_10K.1, U2.31 (PA6_(ADC6))
IR8: IR22.K (C), R19_10K.1, U2.30 (PA7_(ADC7))
IR_PROXIMITY: IR1.K (C), IR2.K (C), IR3.K (C), IR5.K (C), IR6.K (C), IR7.K (C), IR8.K (C), IR14.K (C), Q2.C
IR_SW: R37_10K.1, U2.43 (PB3_(AIN1/OC0))
MISO: SV1.2, U2.2 ((MISO)_PB6)
MOSI: SV1.10, U2.1 ((MOSI)_PB5)
N: JP3.3, POT_10K.2 (S)
unnamed: ENC_LEFT.1 (IN), R20_330E.1
unnamed: C12_0.1PF.1, Q1.1, U2.8 (XTAL1)
unnamed: C11_22PF.1, Q1.2, U2.7 (XTAL2)
unnamed: IR1.A, R4_300E.1
unnamed: IR2.A, R6_300E.1
unnamed: IR3.A, R8_300E.1
unnamed: IR5.A, R10_300E.1
unnamed: LED1.A, R1_1K.2
unnamed: IR6.A, R12_300E.1
unnamed: IR7.A, R14_300E.1
unnamed: IR8.A, R16_300E.1
unnamed: IR14.A, R18_300E.1
unnamed: Q3.B, R36_100K.2, R37_10K.2
unnamed: C1_THROUGHHOLE.1, IC2.1 (VI), JP8.2
unnamed: IC4.4 (O), R24_2K2.1
unnamed: LED2.A, R24_2K2.2
unnamed: IC4.8 (O), R25_2K2.1
unnamed: LED3.A, R25_2K2.2
unnamed: ENC_RIGHT.1 (IN), R22_330E.1
unnamed: LED10_GREEN.A, R41_1K.2
unnamed: IC3.7 (OUT), J1.1, R42_1K.1
unnamed: ENC_RIGHT.4 (OUT), IC4.5 (I), R23_1K.1
unnamed: J1.2, JP7.1
unnamed: Q2.B, Q3.C, R35_10K.1
unnamed: R33_4K7.1, RDIR_B1.A, RDIR_F1.C
unnamed: ENC_LEFT.4 (OUT), IC4.1 (I), R21_1K.1
unnamed: ENC_LEFT.3 (GND_REC), IC4.3 (I)
unnamed: ENC_RIGHT.3 (GND_REC), IC4.9 (I)
unnamed: LED11_RED.A, R42_1K.2
unnamed: BUZ1.+, JP6.2, JP7.2
unnamed: IC3.1 (OUT), JP6.1, R41_1K.1
unnamed: LDIR_B1.A, LDIR_F1.C, R32_4K7.1
unnamed: JP3.15, JP4.2
unnamed: JP4.1, R34_300E.2
OUT1L: C5_0.1UF.1, IC1.3 (1Y), JP2.1, R32_4K7.2
OUT1R: C6_0.1UF.1, IC1.14 (4Y), JP1.1, R33_4K7.2
OUT2L: C7_0.1UF.2, IC1.6 (2Y), JP2.2, LDIR_B1.C, LDIR_F1.A
OUT2R: C8_0.1UF.2, IC1.11 (3Y), JP1.2, RDIR_B1.C, RDIR_F1.A
PIN_26: SV3.7, U2.26 (PC7_(TOSC2))
PIN_40: SV3.8, U2.40 (PB0_(XCK/T0))
PIN_41: SV3.6, U2.41 (PB1_(T1))
PWML: IC1.1 (1-2EN), U2.13 ((OC1B)_PD4)
PWMR: IC1.9 (3-4EN), U2.14 ((OC1A)_PD5)
RESET: JP9.2, LED1.C, SV1.6, U2.4 (~RESET)
RS: JP3.4, U2.19 ((SCL)_PC0)
RW: JP3.5, U2.20 ((SDA)_PC1)
RXD: SV3.3, U2.9 ((RXD)_PD0)
SCK: SV1.4, U2.3 ((SCK)_PB7)
TXD: SV3.5, U2.10 ((TXD)_PD1)
VCC: C2_0.1UF.1, C9_0.1UF.1, IC1.16 (VCC1), IC2.2 (VO), IC3.8 (V+), IC4.14 (VDD), JP3.2, POT_10K.1 (E), R1_1K.1, R4_300E.2, R5_10K.2, R6_300E.2, R7_10K.2, R8_300E.2, R9_10K.2, R10_300E.2, R11_10K.2, R12_300E.2, R13_10K.2, R14_300E.2, R15_10K.2, R16_300E.2, R17_10K.2, R18_300E.2, R19_10K.2, R20_330E.2, R21_1K.2, R22_330E.2, R23_1K.2, R34_300E.1, R35_10K.2, R38_1K.1, SV1.9, SV3.2, U2.5 (VCC_2), U2.17 (VCC_3), U2.27 (AVCC), U2.29 (AREF), U2.38 (VCC)
V_BATT: C3_10UF.1, IC1.8 (VCC2), JP5.1, JP8.1, R2_22K.2, SV3.4

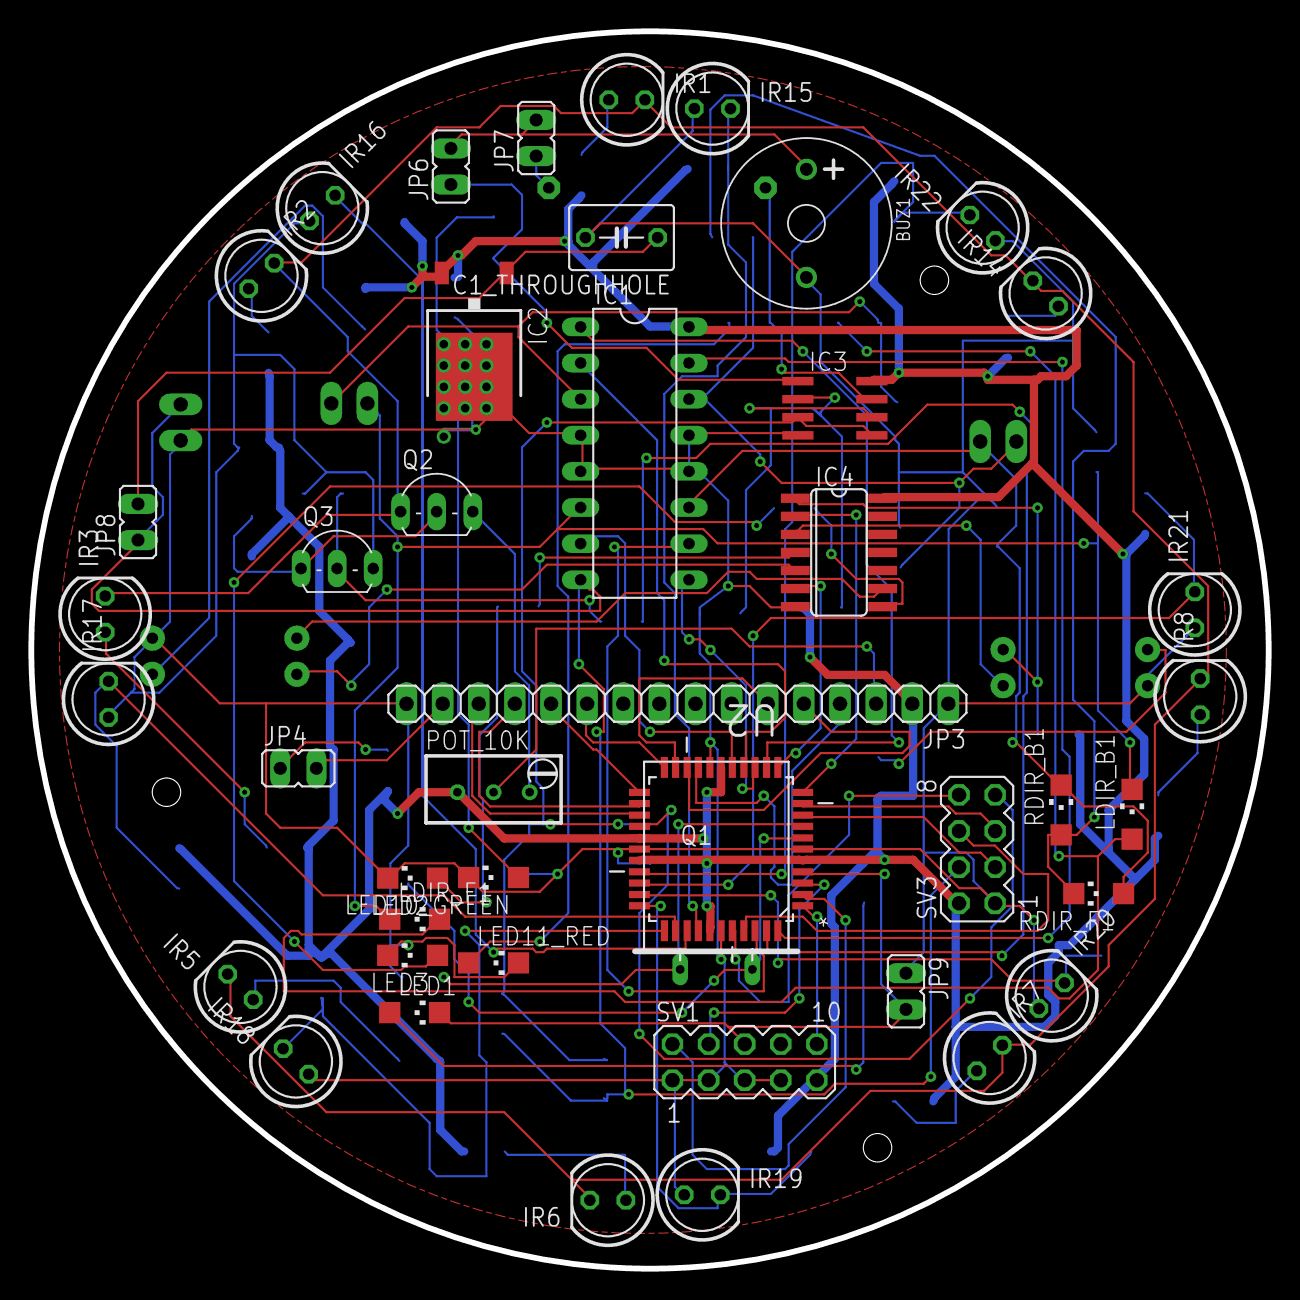
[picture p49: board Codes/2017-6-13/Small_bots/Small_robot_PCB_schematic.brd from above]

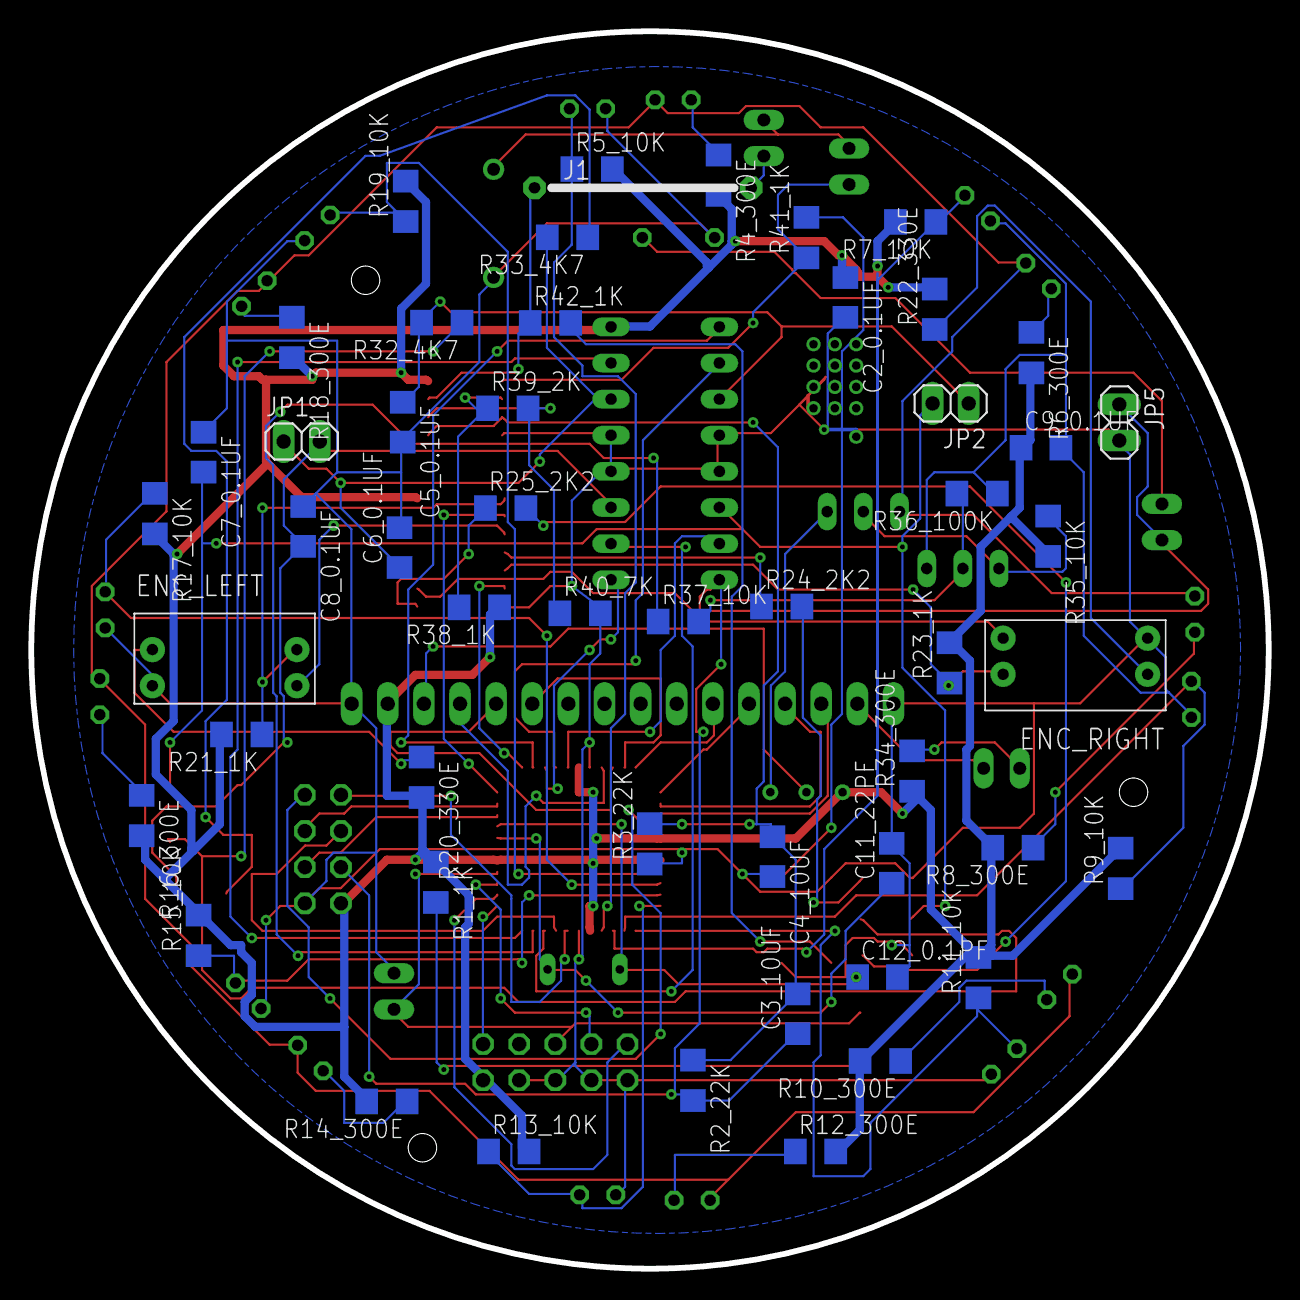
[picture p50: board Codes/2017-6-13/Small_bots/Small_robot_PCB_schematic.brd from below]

Board: 2 copper layers, 87.0 x 87.0 mm, 96 parts (52 on the bottom side), 79 nets.

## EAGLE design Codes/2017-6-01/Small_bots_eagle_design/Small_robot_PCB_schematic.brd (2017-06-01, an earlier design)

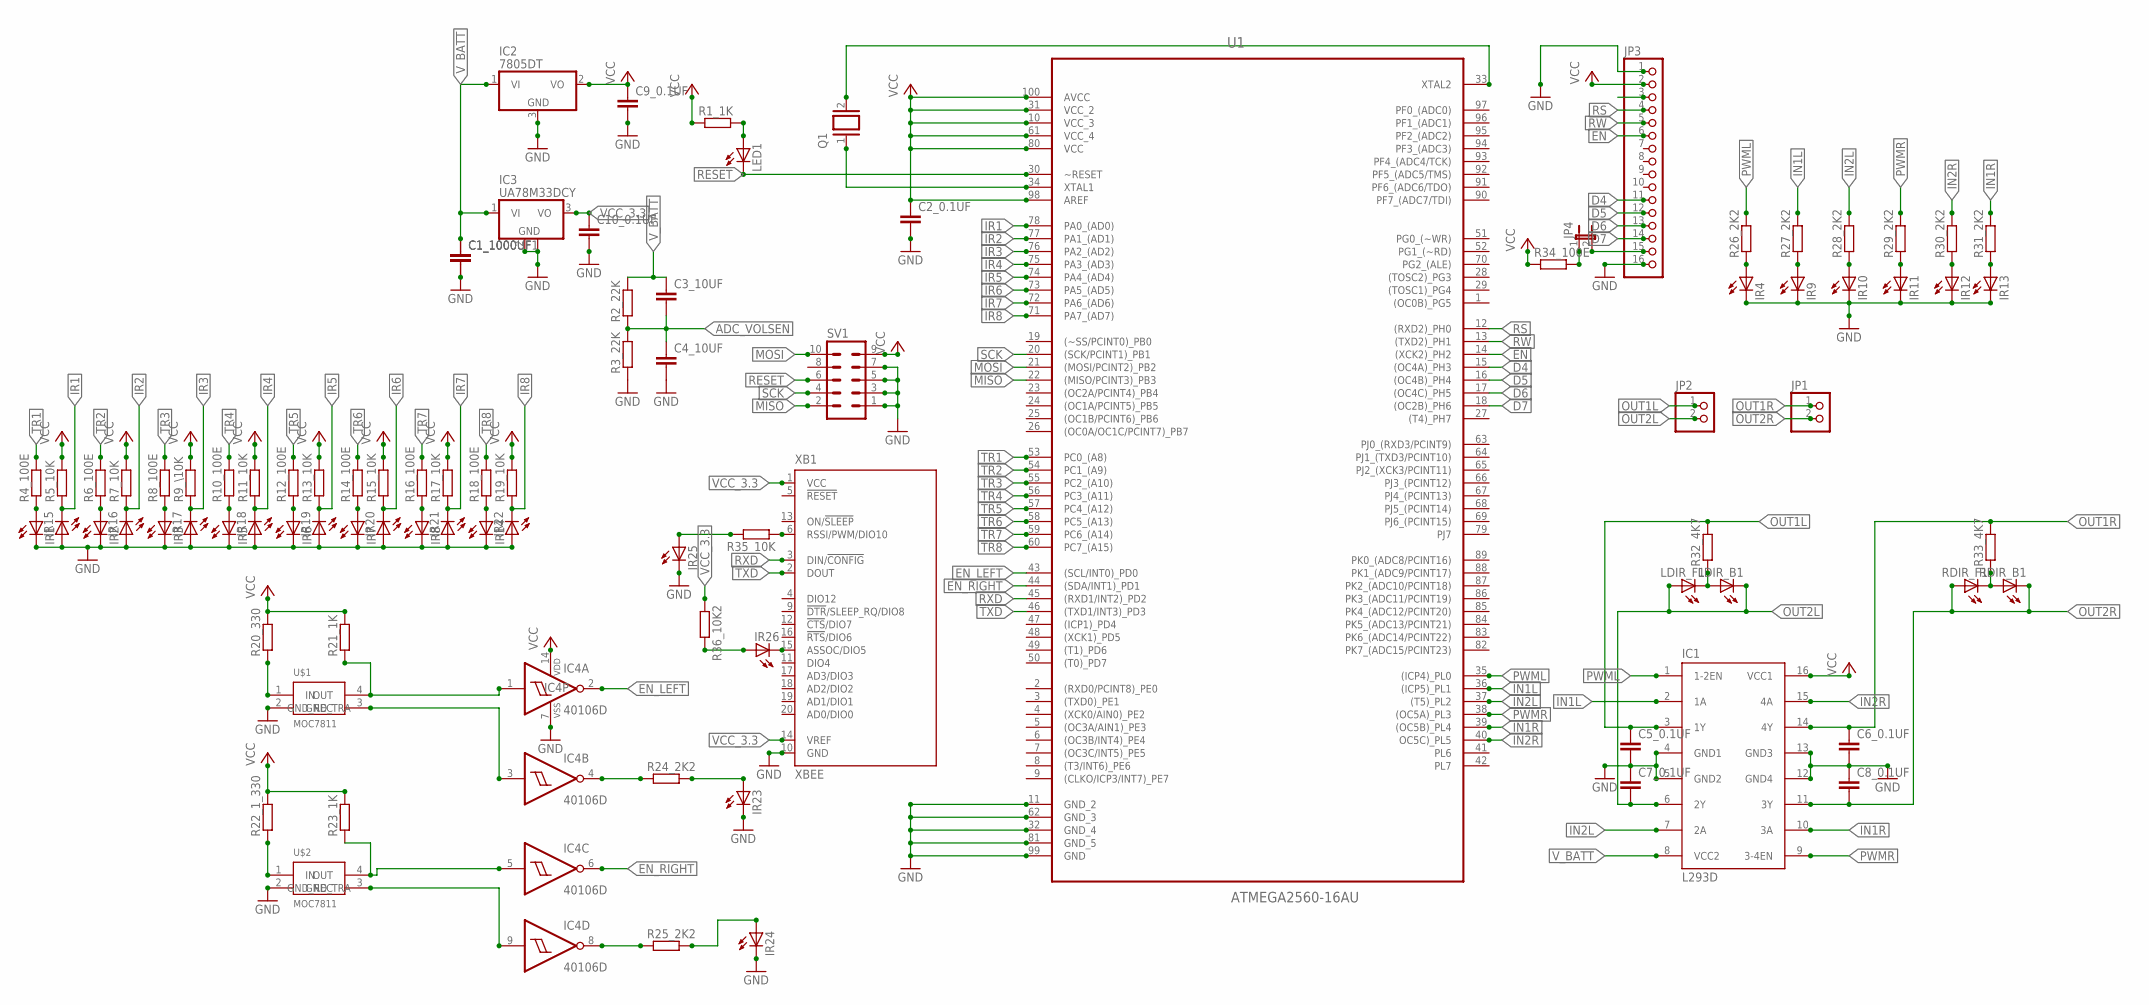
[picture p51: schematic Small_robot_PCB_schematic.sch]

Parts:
C1_1000UF, C1_1000UF1, C2_0.1UF, C3_10UF, C4_10UF, C5_0.1UF, C6_0.1UF, C7_0.1UF, C8_0.1UF, C9_0.1UF, C10_0.1UF: C-EUC1206; C1206
IC1: L293D; DIL16
IC2: 7805DT; TO252
IC3: UA78M33DCY; SOT223
IC4: 40106D; SO14
IR1, IR2, IR3, IR5, IR6, IR7, IR8, IR14, IR15, IR16, IR17, IR18, IR19, IR20, IR21, IR22: LED5MM
IR4, IR9, IR10, IR11, IR12, IR13, IR23, IR24, IR25, IR26: LEDCHIPLED_1206; CHIPLED_1206
JP1, JP2: PINHD-1X2; 1X02
JP3: PINHD-1X16; 1X16
JP4: JP1E; JP1
LDIR_B1: LEDCHIPLED_1206; CHIPLED_1206
LDIR_F1: LEDCHIPLED_1206; CHIPLED_1206
LED1: LEDCHIPLED_1206; CHIPLED_1206
Q1: XTAL; Q
R1_1K, R2_22K, R4_100E, R5_10K, R6_100E, R7_10K, R8_100E, R9_\10K, R10_100E, R11_10K, R12_100E, R13_10K, R14_100E, R15_10K, R16_100E, R17_10K, R18_100E, R19_10K, R20_330, R21_1K, R22_1_330, R23_1K, R24_2K2, R25_2K2, R26_2K2, R27_2K2, R28_2K2, R29_2K2, R30_2K2, R31_2K2, R32_4K7, R33_4K7, R34_100E, R35_10K, R36_10K2: R-EU_R1206; R1206
R3_22K: R-EU_M1206; M1206
RDIR_B1: LEDCHIPLED_1206; CHIPLED_1206
RDIR_F1: LEDCHIPLED_1206; CHIPLED_1206
SV1: MA05-2
U1: ATMEGA2560-16AU; QFP50P1600X1600X120-100N
U$1, U$2: MOC7811; THROUGH_HOLE_NORMAL
XB1: XBEE

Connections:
ADC_VOLSEN: C3_10UF.2, C4_10UF.1, R2_22K.1, R3_22K.2
D4: JP3.11, U1.15 ((OC4A)_PH3)
D5: JP3.12, U1.16 ((OC4B)_PH4)
D6: JP3.13, U1.17 ((OC4C)_PH5)
D7: JP3.14, U1.18 ((OC2B)_PH6)
EN: JP3.6, U1.14 ((XCK2)_PH2)
EN_LEFT: IC4.2 (O), U1.43 ((SCL/INT0)_PD0)
EN_RIGHT: IC4.6 (O), U1.44 ((SDA/INT1)_PD1)
GND: C1_1000UF.2, C1_1000UF1.2, C2_0.1UF.2, C4_10UF.2, C5_0.1UF.2, C6_0.1UF.2, C7_0.1UF.1, C8_0.1UF.1, C9_0.1UF.2, C10_0.1UF.2, IC1.4 (GND1), IC1.5 (GND2), IC1.12 (GND4), IC1.13 (GND3), IC2.3 (GND), IC3.2 (GND), IC3.4 (GND), IC4.7 (VSS), IR1.K (C), IR2.K (C), IR3.K (C), IR4.C, IR5.K (C), IR6.K (C), IR7.K (C), IR8.K (C), IR9.C, IR10.C, IR11.C, IR12.C, IR13.C, IR14.K (C), IR15.A, IR16.A, IR17.A, IR18.A, IR19.A, IR20.A, IR21.A, IR22.A, IR23.C, IR24.C, IR25.C, JP3.1, JP3.16, R3_22K.1, SV1.1, SV1.3, SV1.5, SV1.7, U1.11 (GND_2), U1.32 (GND_4), U1.62 (GND_3), U1.81 (GND_5), U1.99 (GND), U$1.2 (GND_TRA), U$2.2 (GND_TRA), XB1.10 (GND)
IN1L: IC1.2 (1A), R27_2K2.2, U1.36 ((ICP5)_PL1)
IN1R: IC1.10 (3A), R31_2K2.2, U1.39 ((OC5B)_PL4)
IN2L: IC1.7 (2A), R28_2K2.2, U1.37 ((T5)_PL2)
IN2R: IC1.15 (4A), R30_2K2.2, U1.40 (OC5C)_PL5)
IR1: IR15.K (C), R5_10K.1, U1.78 (PA0_(AD0))
IR2: IR16.K (C), R7_10K.1, U1.77 (PA1_(AD1))
IR3: IR17.K (C), R9_\10K.1, U1.76 (PA2_(AD2))
IR4: IR18.K (C), R11_10K.1, U1.75 (PA3_(AD3))
IR5: IR19.K (C), R13_10K.1, U1.74 (PA4_(AD4))
IR6: IR20.K (C), R15_10K.1, U1.73 (PA5_(AD5))
IR7: IR21.K (C), R17_10K.1, U1.72 (PA6_(AD6))
IR8: IR22.K (C), R19_10K.1, U1.71 (PA7_(AD7))
MISO: SV1.2, U1.22 ((MISO/PCINT3)_PB3)
MOSI: SV1.10, U1.21 ((MOSI/PCINT2)_PB2)
N: JP3.3
unnamed: R20_330.1, U$1.1 (IN)
unnamed: Q1.1, U1.34 (XTAL1)
unnamed: Q1.2, U1.33 (XTAL2)
unnamed: IR1.A, R4_100E.1
unnamed: IR2.A, R6_100E.1
unnamed: IR3.A, R8_100E.1
unnamed: IR5.A, R10_100E.1
unnamed: LED1.A, R1_1K.2
unnamed: IR6.A, R12_100E.1
unnamed: IR7.A, R14_100E.1
unnamed: IR8.A, R16_100E.1
unnamed: IR14.A, R18_100E.1
unnamed: IR4.A, R26_2K2.1
unnamed: IC4.4 (O), R24_2K2.1
unnamed: IR23.A, R24_2K2.2
unnamed: IC4.8 (O), R25_2K2.1
unnamed: IR24.A, R25_2K2.2
unnamed: R22_1_330.1, U$2.1 (IN)
unnamed: IR9.A, R27_2K2.1
unnamed: IR10.A, R28_2K2.1
unnamed: IC4.5 (I), R23_1K.1, U$2.4 (OUT)
unnamed: IR11.A, R29_2K2.1
unnamed: IR12.A, R30_2K2.1
unnamed: IR13.A, R31_2K2.1
unnamed: R35_10K.1, XB1.6 (RSSI/PWM/DIO10)
unnamed: R33_4K7.1, RDIR_B1.A, RDIR_F1.C
unnamed: IC4.1 (I), R21_1K.1, U$1.4 (OUT)
unnamed: IC4.3 (I), U$1.3 (GND_REC)
unnamed: IC4.9 (I), U$2.3 (GND_REC)
unnamed: IR25.A, R35_10K.2
unnamed: IR26.C, XB1.15 (ASSOC/DIO5)
unnamed: IR26.A, R36_10K2.2
unnamed: LDIR_B1.A, LDIR_F1.C, R32_4K7.1
unnamed: JP3.15, JP4.2
unnamed: JP4.1, R34_100E.2
OUT1L: C5_0.1UF.1, IC1.3 (1Y), JP2.1, R32_4K7.2
OUT1R: C6_0.1UF.1, IC1.14 (4Y), JP1.1, R33_4K7.2
OUT2L: C7_0.1UF.2, IC1.6 (2Y), JP2.2, LDIR_B1.C, LDIR_F1.A
OUT2R: C8_0.1UF.2, IC1.11 (3Y), JP1.2, RDIR_B1.C, RDIR_F1.A
PWML: IC1.1 (1-2EN), R26_2K2.2, U1.35 ((ICP4)_PL0)
PWMR: IC1.9 (3-4EN), R29_2K2.2, U1.38 ((OC5A)_PL3)
RESET: LED1.C, SV1.6, U1.30 (~RESET)
RS: JP3.4, U1.12 ((RXD2)_PH0)
RW: JP3.5, U1.13 ((TXD2)_PH1)
RXD: U1.45 ((RXD1/INT2)_PD2), XB1.3 (DIN/!CONFIG)
SCK: SV1.4, U1.20 ((SCK/PCINT1)_PB1)
TR1: R4_100E.2, U1.53 (PC0_(A8))
TR2: R6_100E.2, U1.54 (PC1_(A9))
TR3: R8_100E.2, U1.55 (PC2_(A10))
TR4: R10_100E.2, U1.56 (PC3_(A11))
TR5: R12_100E.2, U1.57 (PC4_(A12))
TR6: R14_100E.2, U1.58 (PC5_(A13))
TR7: R16_100E.2, U1.59 (PC6_(A14))
TR8: R18_100E.2, U1.60 (PC7_(A15))
TXD: U1.46 ((TXD1/INT3)_PD3), XB1.2 (DOUT)
VCC: C2_0.1UF.1, C9_0.1UF.1, IC1.16 (VCC1), IC2.2 (VO), IC4.14 (VDD), JP3.2, R1_1K.1, R5_10K.2, R7_10K.2, R9_\10K.2, R11_10K.2, R13_10K.2, R15_10K.2, R17_10K.2, R19_10K.2, R20_330.2, R21_1K.2, R22_1_330.2, R23_1K.2, R34_100E.1, SV1.9, U1.10 (VCC_3), U1.31 (VCC_2), U1.61 (VCC_4), U1.80 (VCC), U1.98 (AREF), U1.100 (AVCC)
VCC_3.3: C10_0.1UF.1, IC3.3 (VO), R36_10K2.1, XB1.1 (VCC), XB1.14 (VREF)
V_BATT: C1_1000UF.1, C1_1000UF1.1, C3_10UF.1, IC1.8 (VCC2), IC2.1 (VI), IC3.1 (VI), R2_22K.2

Board: 2 copper layers, 92 parts (0 on the bottom side), 81 nets, no tracks yet.

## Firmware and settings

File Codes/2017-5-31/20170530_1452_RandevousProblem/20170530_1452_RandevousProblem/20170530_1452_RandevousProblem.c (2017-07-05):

/*
 * _20170530_1452_RandevousProblem.c
 *
 * Created: 30-05-2017 14:53:02
 * Author: R Hariharan
 * Description:
	 The robot can sense the surrounding using IR proximity sensor (8 placed 45 degrees apart). 
	 The centroid of the shape formed by all the robots as vertices is calculated. This is the point the robot travels to.
 */ 

#define F_CPU 14745600
#include <avr/io.h>
#include <avr/interrupt.h>
#include <util/delay.h>
#include <math.h>
#include "lcd.c"
#include "dependency.c"

#define PI 3.14159265

//Function to get the sensor values
void get_sensor_values(int * array)
{
	array[0] = ADC_Conversion(6);
	array[1] = ADC_Conversion(5);
	array[2] = ADC_Conversion(4);
	array[3] = 150;
	array[4] = 150;
	array[5] = 150;
	array[6] = ADC_Conversion(8);
	array[7] = ADC_Conversion(7);
	
	/* array[0] = 150;
	array[1] = 150;
	array[2] = 40;
	array[3] = 150;
	array[4] = 150;
	array[5] = 150;
	array[6] = 150;
	array[7] = 150; */
	return;
}
//Small tweak to atan() function
int attan(int x, int y)
{
	if(x == 0 && y > 0)
	{
		return 90;
	}
	else if(x == 0 && y < 0)
	{
		return 270;
	}
	else
	{
		return atan(y/x) * 180 / PI;
	}
}
//Function computes the centroid of the shape formed by the robots as vertices.
int find_centroid(int * sensor_values,int * centroid)
{
	int x = 0; //x co-ordinate of centroid
	int y = 0; //y co-ordinate of centroid
	int i;
	int counter = 0; //number of robots in the shape (number of vertices)
	//8 Sensor - run loop 8 times
	for(i=0;i<8;i++)
	{
		//Check if robot is in the range 100mm
		if(sensor_values[i] < 100)
		{
			//Convert polar co-ordinates to cartesian co-ordinates
			x += sensor_values[i] * cos(i * 45 * PI / 180);
			y += sensor_values[i] * sin(i * 45 * PI / 180);
			counter++;
		}
	}
	//centroid = (sum of all cordinates)/(number of vetices)
	x = x/(counter+1);
	y = y/(counter+1);
	
	int distance = sqrt(pow(x,2)+pow(y,2)); //Distance of the centroid with robot at (0,0) 
	int angle = attan(x,y); //Angle to rotate by with the robot facing positive x-axis
	//aatan function gives angle of range (90,-90), we need convert it (0,360)
	if(x < 0 && y > 0)
	{
		angle = 90 - angle;
	}
	else if(x < 0 && y < 0)
	{
		angle = 180 + angle;
	}
	centroid[0] = distance;
	centroid[1] = angle;
	return 0;
}

//Print the sensor values on LCD
void print_sensor_values(int * array)
{
	lcd_print(1,5,array[0],3);
	lcd_print(1,9,array[1],3);
	lcd_print(1,13,array[2],3);
	lcd_print(2,5,array[6],3);
	lcd_print(2,9,array[7],3);
	return;
}

//Call the function, and analyse the output
int main(void)
{
	init_devices1();	//To initiate the ports in the device
	init_devices0();	//To initiate the ports in the device
	init_devices2();	//To initiate the ports in the device
	init_devices3();
	lcd_set_4bit();		//To initialise lcd ports
	lcd_init();
    //_delay_ms(5000);
	int bot_sensor_values[8];
	get_sensor_values(bot_sensor_values);
	print_sensor_values(bot_sensor_values);
	int bot_centroid[2];
	find_centroid(bot_sensor_values,bot_centroid);
	lcd_print(2,1,bot_centroid[1],3);
	_delay_ms(2000);
	if(bot_centroid[1] < 0)
	{
		lcd_print(2,5,100,3);
		bot_centroid[1] = 360 + bot_centroid[1];
	}
	lcd_print(1,1,bot_centroid[0],3);
	lcd_print(2,1,bot_centroid[1],3);
	left_degrees(bot_centroid[1]); //Rotate left by the mentioned degrees
	forward_mm(bot_centroid[0]*10); //Move forward by mentioned distance in mm
	
	return 0;
}

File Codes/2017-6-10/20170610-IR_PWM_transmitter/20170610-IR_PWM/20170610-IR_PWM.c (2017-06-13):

/*
 * _20170610_IR_PWM.c
 *
 * Created: 10-06-2017 11:09:24
 *  Author: Hariharan
 */ 

#define F_CPU 14745600
#include <avr/io.h>
#include <avr/interrupt.h>
#include <util/delay.h>
#include <math.h>
#include "lcd.c"
#include "dependency.c"

void turn_on_ir_proximity()
{
	PORTH = PORTH & 0xF7;
} 
void turn_off_ir_proximity()
{
	PORTH = PORTH | 0x08;
}
int main(void)
{
	lcd_set_4bit();		//To initialise lcd ports
	lcd_init();
    while(1)
    {
       turn_off_ir_proximity();
	   _delay_ms(5000);
	   turn_on_ir_proximity();
	   _delay_ms(5000); 
    }
}

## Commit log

2017-05-31 Randevous problem code for firebird, Need to map sensor values properly
    [20170530_1452_RandevousProblem.c, dependency.c]
2017-05-31 Randevous Problem Solved, But need proper sensing values or conversion
    [20170530_1452_RandevousProblem.c]
2017-06-01 Eagle layout without routing done
    [Small_robot_PCB_schematic.brd, Small_robot_PCB_schematic.sch]
2017-06-05 Presentation, IR sensors added properly
2017-06-07 Design of PCB and layout done
    [Small_robot_PCB_schematic.brd, Small_robot_PCB_schematic.sch]
2017-06-08 Componet list of PCB requirement
    [Small_robot_PCB_schematic.csv]
2017-06-09 Final schematic and layout
    [Small_robot_PCB_schematic.brd, Small_robot_PCB_schematic.sch]
2017-06-10 IR switching
2017-06-13 Final PCB for manufacturing
    [Small_robot_PCB_schematic.brd, Small_robot_PCB_schematic.sch]
2017-07-05 PID code commented
2017-07-05 documentation uploaded for editing
    [Small_robot_PCB_schematic.csv]
2017-07-07 Remover Project Report
    [Small_robot_PCB_schematic.csv]
2017-07-07 Final documents
    [Small_robot_PCB_schematic.csv]
